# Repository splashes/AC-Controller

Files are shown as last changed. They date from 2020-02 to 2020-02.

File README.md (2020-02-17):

# P&S Power Electronics AC-Controller
Paul and sabrina AC-Controller and driver board

This is from P&S Power Electronics. I just got the files from them to upload it to GitHub so that whoever is searching for this awesome controller may get the necessary files in one place. Hope this helps someone.

This is the link for MPaulHomes https://github.com/MPaulHolmes

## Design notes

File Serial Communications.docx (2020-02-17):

Serial Communications

To get Realterm, go here:

https://sourceforge.net/projects/realterm/

Then, to set it up, connect the board to the computer with the USB plug. Usually, green is data+, white is data-, red is Vcc, and black is ground.

Next, connect the board to the power supply (The Nissan leaf board uses an external 12v, the chevy volt board uses 12v, the control/driver board uses 24v)

Then, run realterm.

On the “Display” tab, set “Rows” to 40, and click the “Scrollback” box and set it to 2000 for the scrollback.

Now, go to the “Port” tab, and change the “Baud” to 115200. The “Port” should already have detected the right port. Click the “Change” box, so that it will now have the baud rate updated.

Now, click on the black open text box area at the top, and hit enter. You should see a message like “Invalid command. Hit ‘?’ to see a list of valid commands”.

You are now ready to communicate!

current-sensor-amps-per-volt (not needed for the Leaf board/Leaf motor)

The way you use this is, if your current sensor has a feedback of 2.5 volts + 1 volt at “x” amps, then you would type:

current-sensor-amps-per-volt x

So, in the case of the LEM Hass 300-s, the datasheet says that at 0 amps, the current sensor feedback is 2.5v, and at 300 amps, the voltage is about 2.5v + 0.625v. So, the current sensor amps per volt is 300/0.625 amps = 480 amps. So, if you are using a LEM Hass 300-s, you would type:

current-sensor-amps-per-volt 480

If you are using one of the Nissan Leaf control boards with a stock Leaf controller, you would use 400. For the Chevy Volt stock controller, you would use 350.

run-pi-test2 (not needed for the leaf board/leaf motor)

This is the first test that must be done for the motor. It works on all motor types. Start with a battery pack voltage < 100vDC, but at least about 50vDC. If you have no idea about the motor’s characteristics, type

run-pi-test2

It will display a bunch of numbers that are from 0 to around 500. The goal is for the numbers to fall to zero quickly. So, the data might look like this (it always starts at zero. Ignore that one!):

0,500,498,425,402,356,322,300,288,233,188,130,89,63,22,-30,15,-25,44,-12,34,-55,27,…

That would be a good result. It quickly converged, in less than like 30 iterations to around zero. It’s OK that it bounces back and forth once it hits zero.

If you are using a Nissan Leaf motor and my Nissan Leaf control board, don’t worry about this.

kp/ki (not needed for the Leaf board/Leaf motor)

To change the proportional gain of the PI control loop for the torque control, type:

kp xxxxx

To change the integral gain of the PI control loop for torque control, type:

Ki xxxxx

where ‘xxxxx’ is a number from 1 up to 20000. Here’s an example of the usage:
kp 6200

ki 100

For best results, kp should be about 50 or 100 times bigger than ki. Once you have changed kp and ki to a new value, if you want, you can run ‘run-pi-test2’ to see if the results are good.

current-angle-offset

for motor type 2 (permanent magnet with encoder, with one index pulse per mechanical revolution), and motor type 3 (1 index pulse per electrical revolution, which is common when using a resolver. I use this setting for the Nissan Leaf motor and the Remy). The angle offset is the difference between the magnetic north of the motor and the index pulse of the position sensor. You can change it to be in the range of 0 to 511, where the circle is divided up into 512 “degrees”.

This is one of the configurations for the motor that must be done once to find the ideal angle offset. Before doing this procedure, you should find good Kp and Ki values. To do this, follow this procedure:

angle-offset 0

attempt to turn the motor with throttle

angle-offset 20

attempt to turn motor with throttle

…

Keep going until the motor changes directions. Then, reduce the angle offset until the motor no longer turns. The motor may not turn for a range of angle offsets. For example, like this:

angle-offset 138 makes the motor turn clockwise

angle-offset 139 makes the motor not turn at all

angle-offset 140 makes the motor not turn at all

…

angle-offset 163 makes the motor not turn at all

angle-offset 164 makes the motor turn COUNTER-clockwise.

The ideal angle offset for the motor NOT MOVING in this case would be (139 + 163)/2 = 151. What you have found is the absolute WORST angle offset for the motor. Now, to find the ideal angle offset, either add or subtract 128 (the scale is 512 “virtual degrees” in a circle, so 128 “virtual degrees” is the same as 90 real degrees). So, you would type:

angle-offset 279

Or

angle-offset 23

max-regen-position

min-regen-position

min-throttle-position

max-throttle-position

The throttle feedback to the controller will be a signal in 0 to 5v. The controller interprets that as a number from 0 to 1023. The throttle is similar to how they do it on a Tesla and the Nissan Leaf. For some range for the first few % of throttle, it is variable regenerative braking. Somewhere in the middle is zero torque command, and the last bit of throttle is variable positive torque command. So, it might be something like this:

max-regen-position 59

min-regen-position 150

min-throttle-position 220

max-throttle-position 942

100% throttle would be around 942 for the raw feedback, and 0% throttle would have a raw feedback of around 59. Zero torque command would be any raw value in 150 up to 220 in this case.

max-motor-amps

max-motor-amps-regen

This basically sets the maximum torque producing current (Iq) for a permanent magnet motor, and it sets the maximum Id and Iq for an induction motor. This is not battery current, but just current in the motor. You would use it like this:

max-motor-amps 300

max-motor-amps-regen 75

With those settings, you would see 300 amps for Iq in the motor when the throttle is at max-throttle-position. And at zero throttle, you would see -75amps for Iq. So, if you want your car to have very strong regen braking at zero throttle, set the max-motor-amps-regen to something very high. If you want to be thrown back in your seat at takeoff, set max-motor-amps to something very high.

max-battery-amps

max-battery-amps-regen

This sets the maximum current allowed to go into/out of the BATTERIES. You would use it like this:

max-battery-amps 200

max-battery-amps-regen 50

pole-pairs (not needed for the Leaf board/Leaf motor)

this is the number of pole pairs of the motor. One way to find out the number of pole pairs for a permanent magnet motor is to turn the motor shaft at 1 revolution per second, and then measure the Hz on 2 of the phases with a volt meter. It is used for finding the mechanical RPM. Usage:

pole-pairs 4

If you are using a Nissan Leaf motor, the number of pole pairs is 4. But this will already be set if you are using my Leaf control board replacement.

max-rpm

This sets the maximum RPM of the motor shaft. It will hit this, and then bounce against it like in a traditional car (“rev rev rev rev”). Usage:

max-rpm 4500

That would set the max RPM to 4500 RPM.

config

This just shows how the controller is currently configured. Pole pairs, throttle settings, etc… Usage:

config

precharge-time

This sets the time for the precharge delay, in tenths of a second. Example usage:

precharge-time 59

That would set the delay to 5.9 seconds from the time of closing the precharge relay to closing the main contactor. A very safe time delay is 5 RC time constants. The C is the capacitance of your bus capacitor. The R is the resistance of your precharge resistor. So, let’s say you have a bus capacitance of about 1200 microfarad. That means C = 0.0012 Farad. Also, let’s say you are using a 470 Ohm precharge resistor. Then, you would set the precharge time to 5*470*0.0012 seconds = 2.82 seconds. So, you would type:

precharge-time 29

save

One other thing to consider is the energy dissipated in the precharge resistor. You can’t just use any resistor. The total energy during precharge is 0.5 * C * V*V, where C is the bus capacitance, and V is the final bus voltage. Let’s say the bus voltage is 400 volts. So, in our example, the total energy through the resistor is 0.5 * 0.0012 * 400 * 400 Joules = 96 Joules. So, you would need to choose a resistor with a Joule rating greater than 96 Joules. Most resistors don’t list their joule rating, so I just use something from this family of resistors:

https://www.mouser.com/ProductDetail/Ohmite/AY821KE?qs=sGAEpiMZZMvmQ%252bOLa8n%2fMxoZ6mTh6DRODpV4zT6BJZY%3d

data-stream-period

This starts the datastream. You tell it the delay, in milliseconds. Example of usage:

data-stream-period 100

That will start streaming the data that has been enabled for streaming, and will stream it at 100ms intervals. To stop the datastream, type “off”.

stream-raw-throttle

This is one example of enabling something for streaming. This adds the raw throttle to the datastream. Usage:

stream-raw-throttle 1

If you want to remove raw throttle from the datastream, type:

stream-raw-throttle 0

There are lots of things that can be added to the stream. To see a list, type “?”.

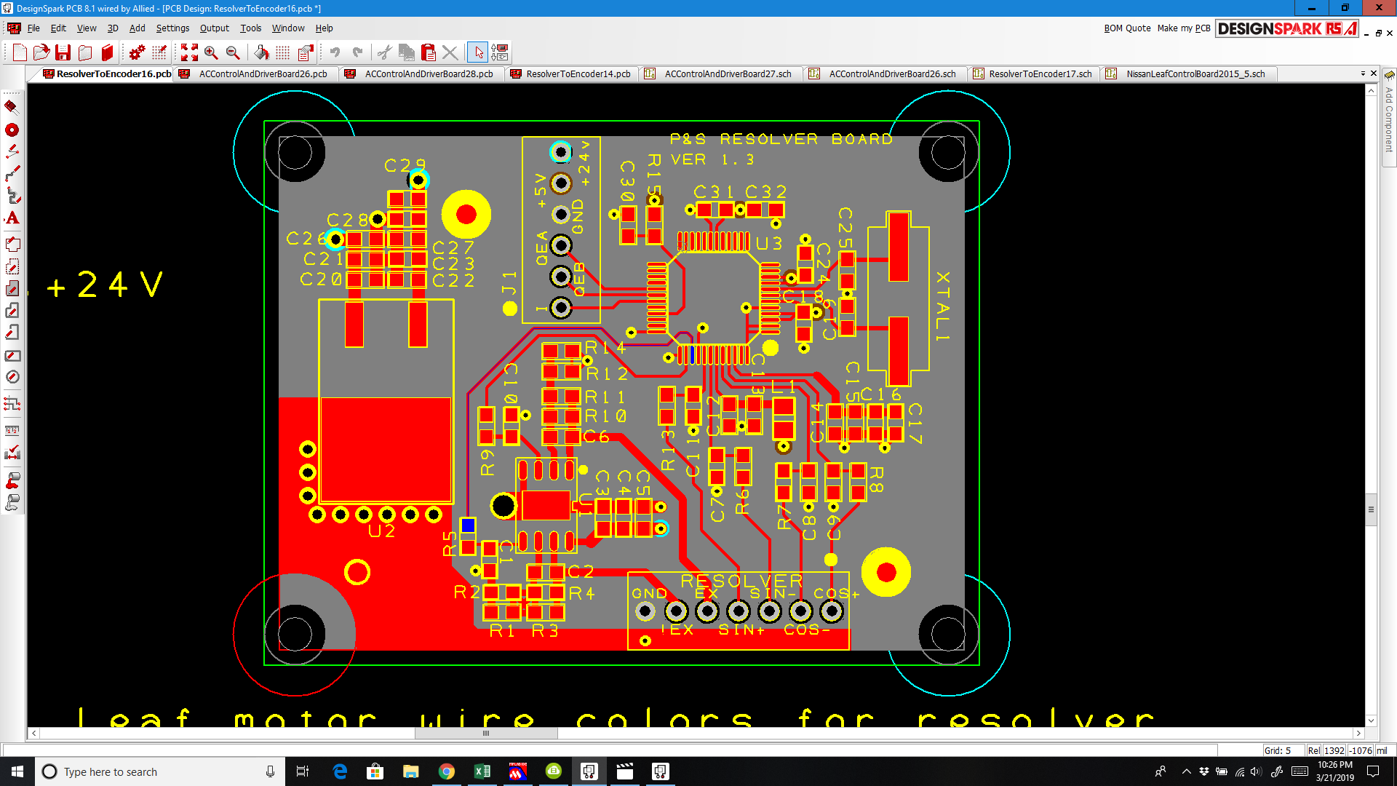
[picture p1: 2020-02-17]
ResolverToEncoder16.png

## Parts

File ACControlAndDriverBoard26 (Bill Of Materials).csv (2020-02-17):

Bill of Materials generated with DesignSpark PCB - www.DesignSpark.com/pcb
--------------------------------------------------------------------------
Ref Name | Component | Value | Package | MPN
Q11 | npn | BC846ALT1G | SOT23 | BC846ALT1G
Q9 | npn | BC846ALT1G | SOT23 | BC846ALT1G
J16 | 6 pin 2x3 |  | USER | 103777-3
U2 | 5v regulator |  | USER | R-78E5.0-1.0
U21 | ATTiny25 | ATTINY25-20SSU | soic8 | ATTINY25-20SSU
C103 | mlcc capacitor | 0.1uF | 1206Standard | C1206C104K5RACTU
C61 | mlcc capacitor | 0.1uF | 1206Standard | C1206C104K5RACTU
C52 | mlcc capacitor | 0.1uF | 1206Standard | C1206C104K5RACTU
C8 | mlcc capacitor | 0.1uF | 1206Standard | C1206C104K5RACTU
C9 | mlcc capacitor | 0.1uF | 1206Standard | C1206C104K5RACTU
C47 | mlcc capacitor | 0.1uF | 1206Standard | C1206C104K5RACTU
C25 | mlcc capacitor | 0.1uF | 1206Standard | C1206C104K5RACTU
C94 | mlcc capacitor | 0.1uF | 1206Standard | C1206C104K5RACTU
C59 | mlcc capacitor | 0.1uF | 1206Standard | C1206C104K5RACTU
C56 | mlcc capacitor | 0.1uF | 1206Standard | C1206C104K5RACTU
C74 | mlcc capacitor | 0.1uF | 1206Standard | C1206C104K5RACTU
C75 | mlcc capacitor | 0.1uF | 1206Standard | C1206C104K5RACTU
C90 | mlcc capacitor | 0.1uF | 1206Standard | C1206C104K5RACTU
C104 | mlcc capacitor | 0.1uF | 1206Standard | C1206C104K5RACTU
C100 | mlcc capacitor | 0.1uF | 1206Standard | C1206C104K5RACTU
C41 | mlcc capacitor | 0.1uF | 1206Standard | C1206C104K5RACTU
C72 | mlcc capacitor | 0.1uF | 1206Standard | C1206C104K5RACTU
C108 | mlcc capacitor | 0.1uF | 1206Standard | C1206C104K5RACTU
C123 | mlcc capacitor | 0.1uF | 1206Standard | C1206C104K5RACTU
C154 | mlcc capacitor | 0.1uF | 1206Standard | C1206C104K5RACTU
C30 | mlcc capacitor | 0.1uF | 1206Standard | C1206C104K5RACTU
C85 | mlcc capacitor | 0.1uF | 1206Standard | C1206C104K5RACTU
C7 | mlcc capacitor | 0.01uF | 1206Standard | 12065C103KAT4A
C42 | mlcc capacitor | 0.01uF | 1206Standard | 12065C103KAT4A
C71 | mlcc capacitor | 0.01uF | 1206Standard | 12065C103KAT4A
C110 | mlcc capacitor | 0.01uF | 1206Standard | 12065C103KAT4A
C122 | mlcc capacitor | 0.01uF | 1206Standard | 12065C103KAT4A
C155 | mlcc capacitor | 0.01uF | 1206Standard | 12065C103KAT4A
C73 | mlcc capacitor | 0.01uF | 1206Standard | 12065C103KAT4A
C60 | mlcc capacitor | 0.01uF | 1206Standard | 12065C103KAT4A
C62 | mlcc capacitor | 0.01uF | 1206Standard | 12065C103KAT4A
C126 | mlcc capacitor | 0.01uF | 1206Standard | 12065C103KAT4A
C6 | mlcc capacitor | 0.01uF | 1206Standard | 12065C103KAT4A
C10 | mlcc capacitor | 0.01uF | 1206Standard | 12065C103KAT4A
C111 | mlcc capacitor | 0.01uF | 1206Standard | 12065C103KAT4A
C95 | mlcc capacitor | 0.01uF | 1206Standard | 12065C103KAT4A
C134 | mlcc capacitor | 0.01uF | 1206Standard | 12065C103KAT4A
C117 | mlcc capacitor | 0.01uF | 1206Standard | 12065C103KAT4A
C109 | mlcc capacitor | 4.7uF 50v | 1206Standard | CGA5L3X7R1H475K160AB
C23 | mlcc capacitor | 4.7uF 50v | 1206Standard | CGA5L3X7R1H475K160AB
C13 | mlcc capacitor | 4.7uF 50v | 1206Standard | CGA5L3X7R1H475K160AB
C16 | mlcc capacitor | 4.7uF 50v | 1206Standard | CGA5L3X7R1H475K160AB
C18 | mlcc capacitor | 4.7uF 50v | 1206Standard | CGA5L3X7R1H475K160AB
C15 | mlcc capacitor | 4.7uF 50v | 1206Standard | CGA5L3X7R1H475K160AB
C12 | mlcc capacitor | 4.7uF 50v | 1206Standard | CGA5L3X7R1H475K160AB
C37 | mlcc capacitor | 4.7uF 50v | 1206Standard | CGA5L3X7R1H475K160AB
C39 | mlcc capacitor | 4.7uF 50v | 1206Standard | CGA5L3X7R1H475K160AB
C40 | mlcc capacitor | 4.7uF 50v | 1206Standard | CGA5L3X7R1H475K160AB
C36 | mlcc capacitor | 4.7uF 50v | 1206Standard | CGA5L3X7R1H475K160AB
C33 | mlcc capacitor | 4.7uF 50v | 1206Standard | CGA5L3X7R1H475K160AB
C32 | mlcc capacitor | 4.7uF 50v | 1206Standard | CGA5L3X7R1H475K160AB
C77 | mlcc capacitor | 4.7uF 50v | 1206Standard | CGA5L3X7R1H475K160AB
C83 | mlcc capacitor | 4.7uF 50v | 1206Standard | CGA5L3X7R1H475K160AB
C76 | mlcc capacitor | 4.7uF 50v | 1206Standard | CGA5L3X7R1H475K160AB
C79 | mlcc capacitor | 4.7uF 50v | 1206Standard | CGA5L3X7R1H475K160AB
C98 | mlcc capacitor | 4.7uF 50v | 1206Standard | CGA5L3X7R1H475K160AB
C106 | mlcc capacitor | 4.7uF 50v | 1206Standard | CGA5L3X7R1H475K160AB
C105 | mlcc capacitor | 4.7uF 50v | 1206Standard | CGA5L3X7R1H475K160AB
C97 | mlcc capacitor | 4.7uF 50v | 1206Standard | CGA5L3X7R1H475K160AB
C99 | mlcc capacitor | 4.7uF 50v | 1206Standard | CGA5L3X7R1H475K160AB
C101 | mlcc capacitor | 4.7uF 50v | 1206Standard | CGA5L3X7R1H475K160AB
C84 | mlcc capacitor | 4.7uF 50v | 1206Standard | CGA5L3X7R1H475K160AB
C80 | mlcc capacitor | 4.7uF 50v | 1206Standard | CGA5L3X7R1H475K160AB
C130 | mlcc capacitor | 4.7uF 50v | 1206Standard | CGA5L3X7R1H475K160AB
C127 | mlcc capacitor | 4.7uF 50v | 1206Standard | CGA5L3X7R1H475K160AB
C135 | mlcc capacitor | 4.7uF 50v | 1206Standard | CGA5L3X7R1H475K160AB
C150 | mlcc capacitor | 4.7uF 50v | 1206Standard | CGA5L3X7R1H475K160AB
C148 | mlcc capacitor | 4.7uF 50v | 1206Standard | CGA5L3X7R1H475K160AB
C153 | mlcc capacitor | 4.7uF 50v | 1206Standard | CGA5L3X7R1H475K160AB
C146 | mlcc capacitor | 4.7uF 50v | 1206Standard | CGA5L3X7R1H475K160AB
C147 | mlcc capacitor | 4.7uF 50v | 1206Standard | CGA5L3X7R1H475K160AB
C149 | mlcc capacitor | 4.7uF 50v | 1206Standard | CGA5L3X7R1H475K160AB
C19 | mlcc capacitor | 4.7uF 50v | 1206Standard | CGA5L3X7R1H475K160AB
C24 | mlcc capacitor | 4.7uF 50v | 1206Standard | CGA5L3X7R1H475K160AB
C34 | mlcc capacitor | 4.7uF 50v | 1206Standard | CGA5L3X7R1H475K160AB
C89 | mlcc capacitor | 4.7uF 50v | 1206Standard | CGA5L3X7R1H475K160AB
C88 | mlcc capacitor | 4.7uF 50v | 1206Standard | CGA5L3X7R1H475K160AB
C102 | mlcc capacitor | 4.7uF 50v | 1206Standard | CGA5L3X7R1H475K160AB
C107 | mlcc capacitor | 4.7uF 50v | 1206Standard | CGA5L3X7R1H475K160AB
C141 | mlcc capacitor | 4.7uF 50v | 1206Standard | CGA5L3X7R1H475K160AB
C152 | mlcc capacitor | 4.7uF 50v | 1206Standard | CGA5L3X7R1H475K160AB
C151 | mlcc capacitor | 4.7uF 50v | 1206Standard | CGA5L3X7R1H475K160AB
C82 | mlcc capacitor | 4.7uF 50v | 1206Standard | CGA5L3X7R1H475K160AB
C65 | mlcc capacitor | 4.7uF 50v | 1206Standard | CGA5L3X7R1H475K160AB
C67 | mlcc capacitor | 4.7uF 50v | 1206Standard | CGA5L3X7R1H475K160AB
C55 | mlcc capacitor | 4.7uF 50v | 1206Standard | CGA5L3X7R1H475K160AB
C128 | mlcc capacitor | 4.7uF 50v | 1206Standard | CGA5L3X7R1H475K160AB
C131 | mlcc capacitor | 4.7uF 50v | 1206Standard | CGA5L3X7R1H475K160AB
C136 | mlcc capacitor | 4.7uF 50v | 1206Standard | CGA5L3X7R1H475K160AB
C140 | mlcc capacitor | 4.7uF 50v | 1206Standard | CGA5L3X7R1H475K160AB
C133 | mlcc capacitor | 4.7uF 50v | 1206Standard | CGA5L3X7R1H475K160AB
C22 | mlcc capacitor | 4.7uF 50v | 1206Standard | CGA5L3X7R1H475K160AB
C21 | mlcc capacitor | 4.7uF 50v | 1206Standard | CGA5L3X7R1H475K160AB
C28 | mlcc capacitor | 4.7uF 50v | 1206Standard | CGA5L3X7R1H475K160AB
C27 | mlcc capacitor | 4.7uF 50v | 1206Standard | CGA5L3X7R1H475K160AB
C86 | mlcc capacitor | 4.7uF 50v | 1206Standard | CGA5L3X7R1H475K160AB
C87 | mlcc capacitor | 4.7uF 50v | 1206Standard | CGA5L3X7R1H475K160AB
C92 | mlcc capacitor | 4.7uF 50v | 1206Standard | CGA5L3X7R1H475K160AB
C91 | mlcc capacitor | 4.7uF 50v | 1206Standard | CGA5L3X7R1H475K160AB
C138 | mlcc capacitor | 4.7uF 50v | 1206Standard | CGA5L3X7R1H475K160AB
C139 | mlcc capacitor | 4.7uF 50v | 1206Standard | CGA5L3X7R1H475K160AB
C144 | mlcc capacitor | 4.7uF 50v | 1206Standard | CGA5L3X7R1H475K160AB
C143 | mlcc capacitor | 4.7uF 50v | 1206Standard | CGA5L3X7R1H475K160AB
C45 | mlcc capacitor | 4.7uF 50v | 1206Standard | CGA5L3X7R1H475K160AB
C31 | mlcc capacitor | 4.7uF 50v | 1206Standard | CGA5L3X7R1H475K160AB
C20 | mlcc capacitor | 4.7uF 50v | 1206Standard | CGA5L3X7R1H475K160AB
C96 | mlcc capacitor | 4.7uF 50v | 1206Standard | CGA5L3X7R1H475K160AB
C124 | mlcc capacitor | 4.7uF 50v | 1206Standard | CGA5L3X7R1H475K160AB
C11 | mlcc capacitor | 4.7uF 50v | 1206Standard | CGA5L3X7R1H475K160AB
C35 | mlcc capacitor | 4.7uF 50v | 1206Standard | CGA5L3X7R1H475K160AB
C44 | mlcc capacitor | 4.7uF 50v | 1206Standard | CGA5L3X7R1H475K160AB
C46 | mlcc capacitor | 4.7uF 50v | 1206Standard | CGA5L3X7R1H475K160AB
C81 | mlcc capacitor | 4.7uF 50v | 1206Standard | CGA5L3X7R1H475K160AB
C26 | mlcc capacitor | 4.7uF 50v | 1206Standard | CGA5L3X7R1H475K160AB
C2 | mlcc capacitor | 4.7uF 50v | 1206Standard | CGA5L3X7R1H475K160AB
C48 | mlcc capacitor | 4.7uF 50v | 1206Standard | CGA5L3X7R1H475K160AB
C63 | mlcc capacitor | 4.7uF 50v | 1206Standard | CGA5L3X7R1H475K160AB
C162 | mlcc capacitor | 4.7uF 50v | 1206Standard | CGA5L3X7R1H475K160AB
C17 | mlcc capacitor | 4.7uF 50v | 1206Standard | CGA5L3X7R1H475K160AB
C113 | mlcc capacitor | 4.7uF 50v | 1206Standard | CGA5L3X7R1H475K160AB
C132 | mlcc capacitor | 4.7uF 50v | 1206Standard | CGA5L3X7R1H475K160AB
C157 | mlcc capacitor | 4.7uF 50v | 1206Standard | CGA5L3X7R1H475K160AB
C51 | mlcc capacitor | 4.7uF 50v | 1206Standard | CGA5L3X7R1H475K160AB
C64 | mlcc capacitor | 4.7uF 50v | 1206Standard | CGA5L3X7R1H475K160AB
C115 | mlcc capacitor | 4.7uF 50v | 1206Standard | CGA5L3X7R1H475K160AB
C119 | mlcc capacitor | 4.7uF 50v | 1206Standard | CGA5L3X7R1H475K160AB
C161 | mlcc capacitor | 4.7uF 50v | 1206Standard | CGA5L3X7R1H475K160AB
C163 | mlcc capacitor | 4.7uF 50v | 1206Standard | CGA5L3X7R1H475K160AB
C49 | mlcc capacitor | 4.7uF 50v | 1206Standard | CGA5L3X7R1H475K160AB
C68 | mlcc capacitor | 4.7uF 50v | 1206Standard | CGA5L3X7R1H475K160AB
C116 | mlcc capacitor | 4.7uF 50v | 1206Standard | CGA5L3X7R1H475K160AB
C120 | mlcc capacitor | 4.7uF 50v | 1206Standard | CGA5L3X7R1H475K160AB
C159 | mlcc capacitor | 4.7uF 50v | 1206Standard | CGA5L3X7R1H475K160AB
C125 | mlcc capacitor | 4.7uF 50v | 1206Standard | CGA5L3X7R1H475K160AB
C114 | mlcc capacitor | 4.7uF 50v | 1206Standard | CGA5L3X7R1H475K160AB
C118 | mlcc capacitor | 4.7uF 50v | 1206Standard | CGA5L3X7R1H475K160AB
C158 | mlcc capacitor | 4.7uF 50v | 1206Standard | CGA5L3X7R1H475K160AB
C38 | mlcc capacitor | 4.7uF 50v | 1206Standard | CGA5L3X7R1H475K160AB
C66 | mlcc capacitor | 30pF | 1206Standard | C1206C300J5GACTU
C70 | mlcc capacitor | 30pF | 1206Standard | C1206C300J5GACTU
C5 | mlcc capacitor | 100pF | 1206Standard | CC1206JRNPO9BN101
C69 | mlcc capacitor | 100pF | 1206Standard | CC1206JRNPO9BN101
C93 | mlcc capacitor | 100pF | 1206Standard | CC1206JRNPO9BN101
C121 | mlcc capacitor | 100pF | 1206Standard | CC1206JRNPO9BN101
C145 | mlcc capacitor | 100pF | 1206Standard | CC1206JRNPO9BN101
C29 | mlcc capacitor | 100pF | 1206Standard | CC1206JRNPO9BN101
C14 | mlcc capacitor | 330pF | 1206Standard | VJ1206Y331KXXCW1BC
C43 | mlcc capacitor | 330pF | 1206Standard | VJ1206Y331KXXCW1BC
C78 | mlcc capacitor | 330pF | 1206Standard | VJ1206Y331KXXCW1BC
C112 | mlcc capacitor | 330pF | 1206Standard | VJ1206Y331KXXCW1BC
C129 | mlcc capacitor | 330pF | 1206Standard | VJ1206Y331KXXCW1BC
C156 | mlcc capacitor | 330pF | 1206Standard | VJ1206Y331KXXCW1BC
C57 | mlcc capacitor | 330pF | 1206Standard | VJ1206Y331KXXCW1BC
C53 | mlcc capacitor | 330pF | 1206Standard | VJ1206Y331KXXCW1BC
C142 | mlcc capacitor | 330pF | 1206Standard | VJ1206Y331KXXCW1BC
C137 | mlcc capacitor | 330pF | 1206Standard | VJ1206Y331KXXCW1BC
C50 | mlcc capacitor | xxx | 1206Standard | DO NOT POPULATE
C54 | mlcc capacitor | xxx | 1206Standard | DO NOT POPULATE
C58 | mlcc capacitor | xxx | 1206Standard | DO NOT POPULATE
C1 | mlcc capacitor | xxx | 1206Standard | DO NOT POPULATE
C160 | mlcc capacitor | xxx | 1206Standard | DO NOT POPULATE
C3 | electrolytic cap | 150-220uF 25v | cap015LS | UHE1E221MPD
C4 | electrolytic cap | 470uF 50v | USER | UPW1H471MHD
L1 | ChokeCommonMode |  |  | SRF0905-102Y
XTAL1 | crystal | 7.3728MHz 20pF |  | ECS-73-20-4XDN
U3 | dc-dc converter | MEV1S2405 |  | MEV1S2405SC
D23 | schottky diode | SS26FL | SOD123w | SS26FL
D28 | schottky diode | SS26FL | SOD123w | SS26FL
D27 | schottky diode | SS26FL | SOD123w | SS26FL
D24 | schottky diode | SS26FL | SOD123w | SS26FL
U18 | dspic30f4011 | DSPIC30F4011-30I/PT | TQFP44 | DSPIC30F4011-30I/PT
U23 | FTDI_FT232RL |  | SSOP | FT232RL-REEL
F1 | Fuse | AF1206F1.60TM | 1206 | AF1206F1.60TM
U6 | GateDriveOptoWithReset | FOD8316 | SOIC16 | FOD8316R2V
U11 | GateDriveOptoWithReset | FOD8316 | SOIC16 | FOD8316R2V
U24 | GateDriveOptoWithReset | FOD8316 | SOIC16 | FOD8316R2V
U19 | GateDriveOptoWithReset | FOD8316 | SOIC16 | FOD8316R2V
U33 | GateDriveOptoWithReset | FOD8316 | SOIC16 | FOD8316R2V
U29 | GateDriveOptoWithReset | FOD8316 | SOIC16 | FOD8316R2V
U31 | HCNR200 | HCNR200-300E | GullWing | HCNR200-300E
ISP | ISP-Interface |  | USER | 3-644456-6
ENCODER | 6 pin male |  | USER | 22-04-1061
 | 6 pin female |  |  | 22-01-1062
U1 | dual mosfet driver | IXDI604SI | soic8_heat_tab | IXDI604SI
U14 | dual mosfet driver | IXDI604SI | soic8_heat_tab | IXDI604SI
U16 | dual mosfet driver | IXDI604SI | soic8_heat_tab | IXDI604SI
U25 | dual mosfet driver | IXDI604SI | soic8_heat_tab | IXDI604SI
U27 | dual mosfet driver | IXDI604SI | soic8_heat_tab | IXDI604SI
U34 | dual mosfet driver | IXDI604SI | soic8_heat_tab | IXDI604SI
CURR1 | 3 pin connector | 3pin Vert Lock | USER | 22-04-1031
CURR3 | 3 pin connector | 3pin Vert Lock | USER | 22-04-1031
CURR2 | 3 pin connector | 3pin Vert Lock | USER | 22-04-1031
TEMP | 3 pin connector | 3pin Vert Lock | USER | 22-04-1031
REV | 3 pin connector | 3pin Vert Lock | USER | 22-04-1031
CAN | 3 pin connector | 3pin Vert Lock | USER | 22-04-1031
BRK | 3 pin connector | 3pin Vert Lock | USER | 22-04-1031
THR | 3 pin connector | 3pin Vert Lock | USER | 22-04-1031
 | female housing 2 OF THESE!! |  |  | 10-11-2153
TRANS1 | Line Filter |  | 13x10mmHoles | PLA10AS3021R3R2B
TRANS2 | Line Filter |  | 13x10mmHoles | PLA10AS3021R3R2B
TRANS3 | Line Filter |  | 13x10mmHoles | PLA10AS3021R3R2B
TRANS4 | Line Filter |  | 13x10mmHoles | PLA10AS3021R3R2B
TRANS5 | Line Filter |  | 13x10mmHoles | PLA10AS3021R3R2B
TRANS6 | Line Filter |  | 13x10mmHoles | PLA10AS3021R3R2B
U5 | comparator | LM293DR | soic8 | LM293DR
U10 | comparator | LM293DR | soic8 | LM293DR
U13 | comparator | LM293DR | soic8 | LM293DR
U8 | comparator | LM293DR | soic8 | LM293DR
U37 | 2.5v voltage regulator | LM4040C25IDBZR | SOT23 | LM4040C25IDBZR
U4 | Quad 2 input NAND |  | SOIC14 | MC74HC00ADR2G
U20 | CAN Transceiver | MCP2551-I/SN | SOIC8 | MCP2551-I/SN
Q1 | NPNTrans | MJD44H11T4 | dpakStandard | MJD44H11T4
Q4 | NPNTrans | MJD44H11T4 | dpakStandard | MJD44H11T5
Q5 | NPNTrans | MJD44H11T4 | dpakStandard | MJD44H11T6
Q10 | NPNTrans | MJD44H11T4 | dpakStandard | MJD44H11T7
Q14 | NPNTrans | MJD44H11T4 | dpakStandard | MJD44H11T8
Q8 | NPNTrans | MJD44H11T4 | dpakStandard | MJD44H11T9
U32 | op amp |  | soic8 | MCP6241T-E/SN
U30 | op amp |  | soic8 | MCP6241T-E/SN
Q2 | PNPTRANS | MJD45H11T4G | dpakStandard | MJD45H11T4G
Q3 | PNPTRANS | MJD45H11T4G | dpakStandard | MJD45H11T4G
Q6 | PNPTRANS | MJD45H11T4G | dpakStandard | MJD45H11T4G
Q7 | PNPTRANS | MJD45H11T4G | dpakStandard | MJD45H11T4G
Q12 | PNPTRANS | MJD45H11T4G | dpakStandard | MJD45H11T4G
Q13 | PNPTRANS | MJD45H11T4G | dpakStandard | MJD45H11T4G
U36 | schottky bridge rectifier |  | SurfaceMount | CDBHM260L-HF
U15 | schottky bridge rectifier |  | SurfaceMount | CDBHM260L-HF
U17 | schottky bridge rectifier |  | SurfaceMount | CDBHM260L-HF
U26 | schottky bridge rectifier |  | SurfaceMount | CDBHM260L-HF
U28 | schottky bridge rectifier |  | SurfaceMount | CDBHM260L-HF
U35 | schottky bridge rectifier |  | SurfaceMount | CDBHM260L-HF
RELAY2 | Relay SPST 1FormA |  | User | G5Q-1A-EL-HA-VH DC24
RELAY1 | Relay SPST 1FormA |  | User | G5Q-1A-EL-HA-VH DC24
R62 | resistor | 1k | 1206Standard | RK73H2BTTE1001F
R38 | resistor | 1k | 1206Standard | RK73H2BTTE1001F
R39 | resistor | 1k | 1206Standard | RK73H2BTTE1001F
R40 | resistor | 1k | 1206Standard | RK73H2BTTE1001F
R41 | resistor | 1k | 1206Standard | RK73H2BTTE1001F
R42 | resistor | 1k | 1206Standard | RK73H2BTTE1001F
R44 | resistor | 1k | 1206Standard | RK73H2BTTE1001F
R45 | resistor | 1k | 1206Standard | RK73H2BTTE1001F
R18 | resistor | 1k | 1206Standard | RK73H2BTTE1001F
R25 | resistor | 1k | 1206Standard | RK73H2BTTE1001F
R60 | resistor | 1k | 1206Standard | RK73H2BTTE1001F
R84 | resistor | 1k | 1206Standard | RK73H2BTTE1001F
R105 | resistor | 2k | 1206Standard | RC1206FR-072KL
R106 | resistor | 2k | 1206Standard | RC1206FR-072KL
R108 | resistor | 2k | 1206Standard | RC1206FR-072KL
R19 | resistor | 2k | 1206Standard | RC1206FR-072KL
R22 | resistor | 2k | 1206Standard | RC1206FR-072KL
R27 | resistor | 2k | 1206Standard | RC1206FR-072KL
R29 | resistor | 2k | 1206Standard | RC1206FR-072KL
R113 | resistor | 2k | 1206Standard | RC1206FR-072KL
R16 | resistor | 2k | 1206Standard | RC1206FR-072KL
R102 | resistor | 2.7 | 1210 | SG73P2ETTD2R70F
R37 | resistor | 2.7 | 1210 | SG73P2ETTD2R70F
R52 | resistor | 2.7 | 1210 | SG73P2ETTD2R70F
R72 | resistor | 2.7 | 1210 | SG73P2ETTD2R70F
R75 | resistor | 2.7 | 1210 | SG73P2ETTD2R70F
R100 | resistor | 2.7 | 1210 | SG73P2ETTD2R70F
R111 | resistor | 2.8k | 1206Standard | RC1206FR-072K8L
R15 | resistor | 3k | 1206Standard | RK73H2BTTD3001F
R24 | resistor | 3k | 1206Standard | RK73H2BTTD3001F
R61 | resistor | 3k | 1206Standard | RK73H2BTTD3001F
R66 | resistor | 3k | 1206Standard | RK73H2BTTD3001F
R80 | resistor | 3k | 1206Standard | RK73H2BTTD3001F
R87 | resistor | 3k | 1206Standard | RK73H2BTTD3001F
R3 | resistor | 3.3Ohm 1w | R0800 | PCF1C3R3K
R4 | resistor | 3.3Ohm 1w | R0800 | PCF1C3R3K
R6 | resistor | 3.3Ohm 1w | R0800 | PCF1C3R3K
R5 | resistor | 3.3Ohm 1w | R0800 | PCF1C3R3K
R7 | resistor | 3.3Ohm 1w | R0800 | PCF1C3R3K
R8 | resistor | 3.3Ohm 1w | R0800 | PCF1C3R3K
R10 | resistor | 3.3Ohm 1w | R0800 | PCF1C3R3K
R9 | resistor | 3.3Ohm 1w | R0800 | PCF1C3R3K
R11 | resistor | 3.3Ohm 1w | R0800 | PCF1C3R3K
R12 | resistor | 3.3Ohm 1w | R0800 | PCF1C3R3K
R14 | resistor | 3.3Ohm 1w | R0800 | PCF1C3R3K
R13 | resistor | 3.3Ohm 1w | R0800 | PCF1C3R3K
R103 | resistor | 3.92k | 1206Standard | RC1206FR-073K92L
R104 | resistor | 4.7k | 1206Standard | RC1206FR-074K7L
R51 | resistor | 4.7k | 1206Standard | RC1206FR-074K7L
R65 | resistor | 4.7k | 1206Standard | RC1206FR-074K7L
R43 | resistor | 4.7k | 1206Standard | RC1206FR-074K7L
R76 | resistor | 4.7k | 1206Standard | RC1206FR-074K7L
R73 | resistor | 4.7k | 1206Standard | RC1206FR-074K7L
R57 | resistor | 4.7k | 1206Standard | RC1206FR-074K7L
R49 | resistor | 4.7k | 1206Standard | RC1206FR-074K7L
R67 | resistor | 4.7k | 1206Standard | RC1206FR-074K7L
R20 | resistor | 4.7k | 1206Standard | RC1206FR-074K7L
R26 | resistor | 4.7k | 1206Standard | RC1206FR-074K7L
R107 | resistor | 10 | 1210 | ESR25JZPF10R0
R31 | resistor | 10 | 1210 | ESR25JZPF10R0
R54 | resistor | 10 | 1210 | ESR25JZPF10R0
R70 | resistor | 10 | 1210 | ESR25JZPF10R0
R77 | resistor | 10 | 1210 | ESR25JZPF10R0
R95 | resistor | 10 | 1210 | ESR25JZPF10R0
R30 | resistor | 10k | 1206Standard | RC1206FR-0710KL
R23 | resistor | 10k | 1206Standard | RC1206FR-0710KL
R63 | resistor | 10k | 1206Standard | RC1206FR-0710KL
R110 | resistor | 10k | 1206Standard | RC1206FR-0710KL
R17 | resistor | 10k | 1206Standard | RC1206FR-0710KL
R28 | resistor | 10k | 1206Standard | RC1206FR-0710KL
R56 | resistor | 10k | 1206Standard | RC1206FR-0710KL
R68 | resistor | 10k | 1206Standard | RC1206FR-0710KL
R79 | resistor | 10k | 1206Standard | RC1206FR-0710KL
R91 | resistor | 10k | 1206Standard | RC1206FR-0710KL
R58 | resistor | 10k | 1206Standard | RC1206FR-0710KL
R69 | resistor | 10k | 1206Standard | RC1206FR-0710KL
R112 | resistor | 22k | 1206Standard | RC1206FR-0722KL
R92 | resistor | 27k | 1210Standard | RC1210FR-0727KL
R90 | resistor | 27k | 1210Standard | RC1210FR-0727KL
R89 | resistor | 27k | 1210Standard | RC1210FR-0727KL
R94 | resistor | 27k | 1210Standard | RC1210FR-0727KL
R99 | resistor | 27k | 1210Standard | RC1210FR-0727KL
R97 | resistor | 27k | 1210Standard | RC1210FR-0727KL
R88 | resistor | 27k | 1210Standard | RC1210FR-0727KL
R86 | resistor | 27k | 1210Standard | RC1210FR-0727KL
R96 | resistor | 27k | 1210Standard | RC1210FR-0727KL
R93 | resistor | 27k | 1210Standard | RC1210FR-0727KL
R109 | resistor | 47k | 1206Standard | RC1206FR-0747KL
R32 | resistor | 47k | 1206Standard | RC1206FR-0747KL
R55 | resistor | 47k | 1206Standard | RC1206FR-0747KL
R71 | resistor | 47k | 1206Standard | RC1206FR-0747KL
R78 | resistor | 47k | 1206Standard | RC1206FR-0747KL
R98 | resistor | 47k | 1206Standard | RC1206FR-0747KL
R34 | resistor | 47k | 1206Standard | RC1206FR-0747KL
R47 | resistor | 47k | 1206Standard | RC1206FR-0747KL
R85 | resistor | 47k | 1206Standard | RC1206FR-0747KL
R81 | resistor | 47k | 1206Standard | RC1206FR-0747KL
R59 | resistor | 47k | 1206Standard | RC1206FR-0747KL
R46 | resistor | 47k | 1206Standard | RC1206FR-0747KL
R48 | resistor | 47k | 1206Standard | RC1206FR-0747KL
R35 | resistor | 47k | 1206Standard | RC1206FR-0747KL
R36 | resistor | 47k | 1206Standard | RC1206FR-0747KL
R33 | resistor | 47k | 1206Standard | RC1206FR-0747KL
R2 | resistor | 100 | 1206Standard | RC1206FR-07100RL
R21 | resistor | 100 | 1206Standard | RC1206FR-07100RL
R50 | resistor | 100 | 1206Standard | RC1206FR-07100RL
R64 | resistor | 100 | 1206Standard | RC1206FR-07100RL
R74 | resistor | 100 | 1206Standard | RC1206FR-07100RL
R83 | resistor | 100 | 1206Standard | RC1206FR-07100RL
R53 | resistor | 120 Ohm | 1210Standard | RC1210FR-07120RL
R82 | resistor | 330 | 1206Standard | RC1206FR-07330RL
R1 | resistor | xxx | 1206Standard | DO NOT POPULATE
R101 | resistor | xxx | 1206Standard | DO NOT POPULATE
U12 | SN74HC08 | SN74HC08D | SO14NB | SN74HC08D
U22 | SN74HC08 | SN74HC08D | SO14NB | SN74HC08D
U7 | SN74HC21 | SN74HC21D | SO14NB | SN74HC21D
U9 | SN74HC21 | SN74HC21D | SO14NB | SN74HC21D
J14 | SpadeConnector |  | FEMALE_0-11 | 534-3534 | mouser part number
J4 | SpadeConnector |  | FEMALE_0-11 | 534-3534 | mouser part number
J15 | SpadeConnector |  | FEMALE_0-11 | 534-3534 | mouser part number
J1 | SpadeConnector |  | FEMALE_0-11 | 534-3534 | mouser part number
J2 | SpadeConnector |  | FEMALE_0-11 | 534-3534 | mouser part number
J5 | SpadeConnector |  | FEMALE_0-11 | 534-3534 | mouser part number
J3 | SpadeConnector |  | FEMALE_0-11 | 534-3534 | mouser part number
J8 | SpadeConnector |  | FEMALE_0-11 | 534-3534 | mouser part number
J6 | SpadeConnector |  | FEMALE_0-11 | 534-3534 | mouser part number
J7 | SpadeConnector |  | FEMALE_0-11 | 534-3534 | mouser part number
J9 | SpadeConnector |  | FEMALE_0-11 | 534-3534 | mouser part number
J12 | SpadeConnector |  | FEMALE_0-11 | 534-3534 | mouser part number
J10 | SpadeConnector |  | FEMALE_0-11 | 534-3534 | mouser part number
J11 | SpadeConnector |  | FEMALE_0-11 | 534-3534 | mouser part number
J13 | SpadeConnector |  | FEMALE_0-11 | 534-3534 | mouser part number
VIN | SpadeConnector |  | FEMALE_0-11 | 534-3534 | mouser part number
GND | SpadeConnector |  | FEMALE_0-11 | 534-3534 | mouser part number
CIN | SpadeConnector |  | FEMALE_0-11 | 534-3534 | mouser part number
PCOUT | SpadeConnector |  | FEMALE_0-11 | 534-3534 | mouser part number
COUT | SpadeConnector |  | FEMALE_0-11 | 534-3534 | mouser part number
HVGND | SpadeConnector |  | FEMALE_0-11 | 534-3534 | mouser part number
HV | SpadeConnector |  | FEMALE_0-11 | 534-3534 | mouser part number
D1 | diode | 1000V Ultrafast | 0_45Inch | UF4007
D6 | diode | 1000V Ultrafast | 0_45Inch | UF4007
D11 | diode | 1000V Ultrafast | 0_45Inch | UF4007
D16 | diode | 1000V Ultrafast | 0_45Inch | UF4007
D25 | diode | 1000V Ultrafast | 0_45Inch | UF4007
D32 | diode | 1000V Ultrafast | 0_45Inch | UF4007
USB | USB_TYPE_B |  | USER | 67068-8110
D3 | ZenerDiode | 8.2v 5w | SMB | 3SMAJ5923B-TP
D9 | ZenerDiode | 8.2v 5w | SMB | 3SMAJ5923B-TP
D13 | ZenerDiode | 8.2v 5w | SMB | 3SMAJ5923B-TP
D19 | ZenerDiode | 8.2v 5w | SMB | 3SMAJ5923B-TP
D29 | ZenerDiode | 8.2v 5w | SMB | 3SMAJ5923B-TP
D35 | ZenerDiode | 8.2v 5w | SMB | 3SMAJ5923B-TP
D7 | ZenerDiode | 17V 5W | SMB | 1SMB5930BT3G
D15 | ZenerDiode | 17V 5W | SMB | 1SMB5930BT3G
D33 | ZenerDiode | 17V 5W | SMB | 1SMB5930BT3G
D31 | ZenerDiode | 17V 5W | SMB | 1SMB5930BT3G
D17 | ZenerDiode | 17V 5W | SMB | 1SMB5930BT3G
D5 | ZenerDiode | 17V 5W | SMB | 1SMB5930BT3G
D4 | ZenerDiode | 17V 5W | SMB | 1SMB5930BT3G
D8 | ZenerDiode | 17V 5W | SMB | 1SMB5930BT3G
D18 | ZenerDiode | 17V 5W | SMB | 1SMB5930BT3G
D14 | ZenerDiode | 17V 5W | SMB | 1SMB5930BT3G
D34 | ZenerDiode | 17V 5W | SMB | 1SMB5930BT3G
D30 | ZenerDiode | 17V 5W | SMB | 1SMB5930BT3G
D2 | ZenerDiode | 24v Zener | SMB | 1SMB5934BT3G
D10 | ZenerDiode | 24v Zener | SMB | 1SMB5934BT3G
D12 | ZenerDiode | 24v Zener | SMB | 1SMB5934BT3G
D22 | ZenerDiode | 24v Zener | SMB | 1SMB5934BT3G
D26 | ZenerDiode | 24v Zener | SMB | 1SMB5934BT3G
D36 | ZenerDiode | 24v Zener | SMB | 1SMB5934BT3G
D20 | schottky diode | MBRAF360T3G | SMB | MBRAF360T3G
D21 | TVS diode | SMA6J24A-TP | SMB | SMA6J24A-TP

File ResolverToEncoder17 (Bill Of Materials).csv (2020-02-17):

Bill of Materials generated with DesignSpark PCB - www.DesignSpark.com/pcb
--------------------------------------------------------------------------
Ref Name | Component | Value | Package | MPN
RESOLVER | 7 pin connector |  | USER | 22-04-1071
 | 7pin female housing |  |  | 22-01-1072
 | 6pin connector |  |  | 22-04-1061
 | 6pin female housing |  |  | 22-01-1062
 | crimp pins 13 of these!! |  |  | 08-50-0114
U1 | 7805Replacement |  | D2PAK | MC7812ABD2TG
C9 | Capacitor0.2-MLCC | 0.1uF | 1206Standard | C1206C104K5RACTU
C3 | Capacitor0.2-MLCC | 0.1uF | 1206Standard | C1206C104K5RACTU
C1 | Capacitor0.2-MLCC | 0.1uF | 1206Standard | C1206C104K5RACTU
C2 | Capacitor0.2-MLCC | 0.1uF | 1206Standard | C1206C104K5RACTU
C4 | Capacitor0.2-MLCC | 0.1uF | 1206Standard | C1206C104K5RACTU
C15 | Capacitor0.2-MLCC | 0.01uF | 1206Standard | 12065C103KAT4A
C14 | Capacitor0.2-MLCC | 0.01uF | 1206Standard | 12065C103KAT4A
C18 | Capacitor0.2-MLCC | 0.01uF | 1206Standard | 12065C103KAT4A
C22 | Capacitor0.2-MLCC | 0.01uF | 1206Standard | 12065C103KAT4A
C11 | Capacitor0.2-MLCC | 4.7uF | 1206Standard | CGA5L3X7R1H475K160AB
C19 | Capacitor0.2-MLCC | 4.7uF | 1206Standard | CGA5L3X7R1H475K160AB
C17 | Capacitor0.2-MLCC | 4.7uF | 1206Standard | CGA5L3X7R1H475K160AB
C23 | Capacitor0.2-MLCC | 4.7uF | 1206Standard | CGA5L3X7R1H475K160AB
C13 | Capacitor0.2-MLCC | 4.7uF | 1206Standard | CGA5L3X7R1H475K160AB
C25 | Capacitor0.2-MLCC | 4.7uF | 1206Standard | CGA5L3X7R1H475K160AB
C10 | Capacitor0.2-MLCC | 4.7uF | 1206Standard | CGA5L3X7R1H475K160AB
C20 | Capacitor0.2-MLCC | 30pF | 1206Standard | C1206C300J5GACTU
C21 | Capacitor0.2-MLCC | 30pF | 1206Standard | C1206C300J5GACTU
C12 | Capacitor0.2-MLCC | 2200pF | 1206Standard | VJ1206Y222MXXPW1BC
C16 | Capacitor0.2-MLCC | 2200pF | 1206Standard | VJ1206Y222MXXPW1BC
C26 | Capacitor0.2-MLCC | 2200pF | 1206Standard | VJ1206Y222MXXPW1BC
C8 | Capacitor0.2-MLCC | 2200pF | 1206Standard | VJ1206Y222MXXPW1BC
C24 | Capacitor0.2-MLCC | 2200pF | 1206Standard | VJ1206Y222MXXPW1BC
C7 | Capacitor0.2-MLCC | 2200pF | 1206Standard | VJ1206Y222MXXPW1BC
C6 | Capacitor0.2-MLCC | 2200pF | 1206Standard | VJ1206Y222MXXPW1BC
C5 | Capacitor0.2-MLCC | 2200pF | 1206Standard | VJ1206Y222MXXPW1BC
XTAL1 | CRYSTAL-8MHz | 8.192MHz | USER | XT9S20ANA8M
U2 | DualOpAmp |  | soicWithHeat | AD8397ARDZ-REEL7
J1 | encoder |  | USER | 22-04-1061
L1 | ferrite |  | 0805Standard | MMZ2012R102AT000
R1 | Resistor-0.25watt | 1k | 1206Standard | RK73H2BTTE1001F
R6 | Resistor-0.25watt | 1k | 1206Standard | RK73H2BTTE1001F
R8 | Resistor-0.25watt | 1k | 1206Standard | RK73H2BTTE1001F
R9 | Resistor-0.25watt | 1k | 1206Standard | RK73H2BTTE1001F
R11 | Resistor-0.25watt | 1k | 1206Standard | RK73H2BTTE1001F
R10 | Resistor-0.25watt | 1k | 1206Standard | RK73H2BTTE1001F
R2 | Resistor-0.25watt | 1k | 1206Standard | RK73H2BTTE1001F
R5 | Resistor-0.25watt | 1k | 1206Standard | RK73H2BTTE1001F
R4 | Resistor-0.25watt | 2.2k | 1206Standard | RK73H2BTTD2201F
R3 | Resistor-0.25watt | 2.2k | 1206Standard | RK73H2BTTD2201F
R7 | Resistor-0.25watt | 4.7k | 1206Standard | RC1206FR-074K7L
U3 | ResolverToEncoder-AD2S1210 |  | TQFP-48 | AD2S1210ASTZ

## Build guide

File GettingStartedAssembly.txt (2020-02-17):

Hello!  OK, let's start with the PDF.  The default is to use a hall effect throttle.  You can use either needle nose pliers and a little dab of solder, or a proper crimping tool like this (there may be a cheap chinese equivalent, but I'm not sure):
https://www.amazon.com/Engineer-PA-09-Micro-Connector-Crimpers/dp/B002AVVO7K

For the power section, I would suggest plugging in your board to 3 IGBT half bridges, and then placing the IGBTs/board on an aluminum plate and then mark the 12 IGBT holes.  Then you can drill the 12 holes with a hand drill and once they are fixed, all you need to do is add a B+ and B- copper sheet that bolts to the 3 B+ and B- points on the IGBTs (see the PDF).  I recommend making the copper sheets so the cross section is like this:  ][.  Then put an isolation between the 2 sheets.  Something like Kapton tape, or nomex paper.  So it would be like this:  ]|[.  ] would be B+, [ would be B-, and | would be the nomex paper or Kapton tape.  The idea is to bolt on the capacitor(s) upside down to B+ and B- sheets, and also bolt the sheets to all 3 IGBT half bridges.

I would suggest these capacitors in terms of easiness to work with:
http://www.mouser.com/ProductDetail/Kemet/C4DEFPQ6380A8TK/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

3 will fit, but It all depends on what power requirement you have.  Alternatively, I would get this:
http://www.sbelectronics.com/product/700d348-power-ring/
It's more mechanically awkward, but is capable of higher power.

next, decide what current sensors you are going to use.  What is the maximum current your motor will see?  I recommend Lem Hass 50-s, 100-s, 200-s, 300-s, 400-s current sensors.  Depending on the sort of current sensor and where you mount them, will determine how you will build your current sensor cables.  I suggest 3 of them for extra safety.

The board needs +24v for power.  To get that I would suggest this:
http://www.mouser.com/ProductDetail/Mean-Well/SD-15A-24/?qs=sGAEpiMZZMvGsmoEFRKS8N2RkxUSJnDinUf%252b7ghl12k%3d

Then you can use the car's +12v auxiliary battery for powering the DC-DC, which in turn powers the board.

 I'm putting together a video assembly, but it's not done.  One possible assembly process is here (specifically designed around the 16 tab ring capacitor):
http://www.instructables.com/id/200kW-AC-Motor-Controller-for-Electric-Car/

-Paul

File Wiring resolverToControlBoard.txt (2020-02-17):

Notice the writing for the pinouts for the resolver board.  The 7 pin connector goes:

See the attached ResolverToEncoder17Pinout.pdf.

The following goes to the resolver:
GND (this is optional, but would be connected to the shield of a 7 pin shielded cable).
!EX 
EX 
SIN+ 
SIN-
COS-
COS+

The following goes to the control/driver board:
+24v
+5v
GND
QEA
QEB
I (this is short of index)

On the control/driver board, see the pinout attached.  The view of the ACControlDriver26Pinout.pdf is of the top of the board, which is the surface mount components.  See the 6 connections on that board called:
Encoder +24v
Encoder +5v
Encoder GND
Encoder QEA
Encoder QEB
Encoder INDEX

Those pins go to the resolver to encoder board's 6 pin connector.

-Paul

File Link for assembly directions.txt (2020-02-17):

https://www.dropbox.com/s/7umzxa6tubatd9y/20170515_180213.zip?dl=0

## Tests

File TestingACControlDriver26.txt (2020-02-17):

Testing your newly soldered board:

Connect the 3 current sensors.

Jumper together J2/J3/J14, J7/J8/J15, and J11/J12/J4 (this disables the desaturation detection circuit, to allow the PWM to get through for testing)

Connect an AVRISP MKii (or some other avr programmer) to J41.  

Attach +24v to J38, and the 24v ground to J39.  
Program the ATTiny25 with DC-DC-Converter.hex.  You will need Atmel Studio, which is free, and something like an AVR isp mkii, or some other AVR programmer.
With power still attached, measure the voltage between each pair of back metal tabs of Q3/Q4, Q5/Q6, Q7/Q8, Q9/Q10, Q11/Q12, Q13/Q14.
You should get around 24v (+/-) for each measurement.  If you don't, check your soldering!
Disconnect 24v power.  Remove the AVRISP MKii.

Attach PICKit3.  
**Optional Extra step if you have MPLab installed, and can compile the AC controller software**
uncomment the line "#define DEBUG_MODE" in ACController.h.
Compile and program (in release mode) the dsPIC30F4011.  Measure the voltage from 0v to each of "GATE" across the top of the board. You should get around 3v each time.
Now, comment out the line "define DEBUG_MODE", so it looks like this:
// #define DEBUG_MODE
rather than
#define DEBUG_MODE
And then recompile the code and program the chip.  You are done!
**End of optional extra step**

Program the dsPIC30F4011 with the provided .hex file.  It will be called something like ACController.hex. Put the negative
probe of the volt meter on any of the test points across the top labeled 0v.  They are all connected right now because of the jumper wires you added.
With the positive lead of the volt meter, measure all the test points labeled "GATE". It should alternate -8v & 15v as you go left to right, measuring
"GATE" of all 6 isolated supplies.

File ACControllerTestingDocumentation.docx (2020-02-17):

AC Controller testing with Nissan Leaf Motor (or any motor that has a resolver whose lobes match the number of pole pairs of the motor)

If your control/driver board was completed by me, it has already been tested. First, let’s verify the wiring to the controller. This is a picture of the surface mount side of the most recent controller (ACControlDriver27.pcb):

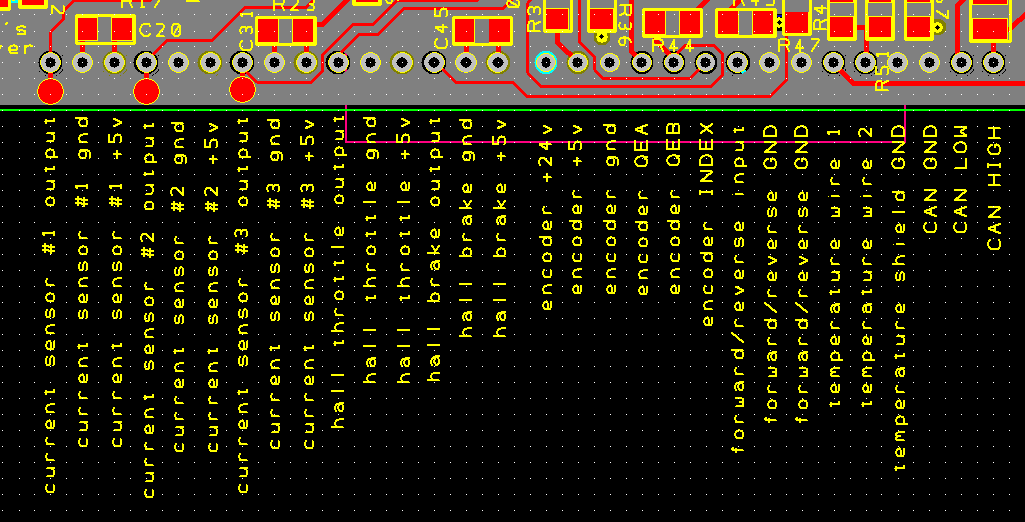
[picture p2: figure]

You need to build 3 current sensor cables. Let’s say you are using a LEM Hass 200-s. This will give a peak current range of -400amp to +400amp for the phases. Here’s the datasheet for the LEM Hass:

https://www.lem.com/sites/default/files/products_datasheets/hass_50_600-s.pdf

Pay attention to the pinout of the current sensor and the pinout of the control board. The current sensor has 4 pins, but you only need pin 2 (current sensor output), pin 3 (ground), and pin 4 (+5v). Pin 1 is not used, so there’s nowhere to plug it into the control board. So, you will need three 4 pin housings like this to mate to the 3 current sensors:

https://www.mouser.com/ProductDetail/Molex/22-01-1042?qs=5gBG3L055oM6gq%2fgjbx3Gw%3d%3d

And these pins:

https://www.mouser.com/ProductDetail/Molex/08-50-0114?qs=%2fha2pyFadujh2f7KQ%252bXWe2d6E0tCKKZpLCtYbdvIlLc%3d

The other end of the current sensor wire can use the same crimp pins too. You will need a total of 18 for the current sensor cables (none in the unused hole). Make sure you twist the 3 wires together for the current sensor cable to reduce noise. Use 22awg or 24awg wire. A drill works well for twisting the wires together. A shielded cable with the drain wire connected to the ground on one end works well too:

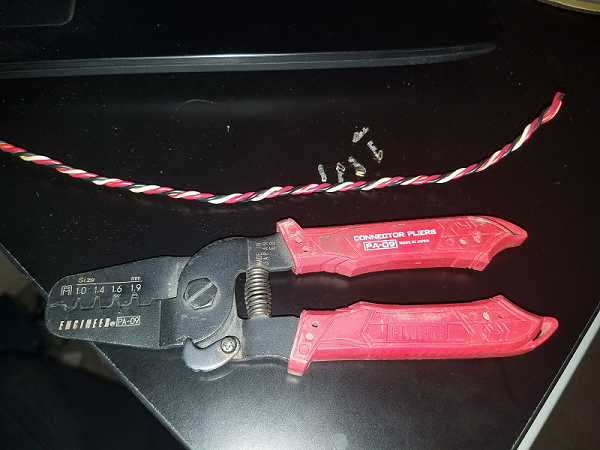
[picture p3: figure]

I use the 1.6 and the 1.9 mm for the crimping.

Next you will need a hall effect throttle like this:

https://www.ebay.com/itm/Throttle-PB-6-Type-0-5V-Hall-Effect-Throttle-Box-generic-/110658990971

You can get a 2nd one for the brakes if you like, but as of ver. 1.0 of the software, the brake regen is disabled. You only get regen from releasing the throttle. The brake regen will be added most likely in the next software release.

If you are using a resolver to encoder board, you will need to connect the 6 encoder pins on the control board (+24v, +5v, gnd, QEA, QEB, INDEX) to the resolver to encoder board:

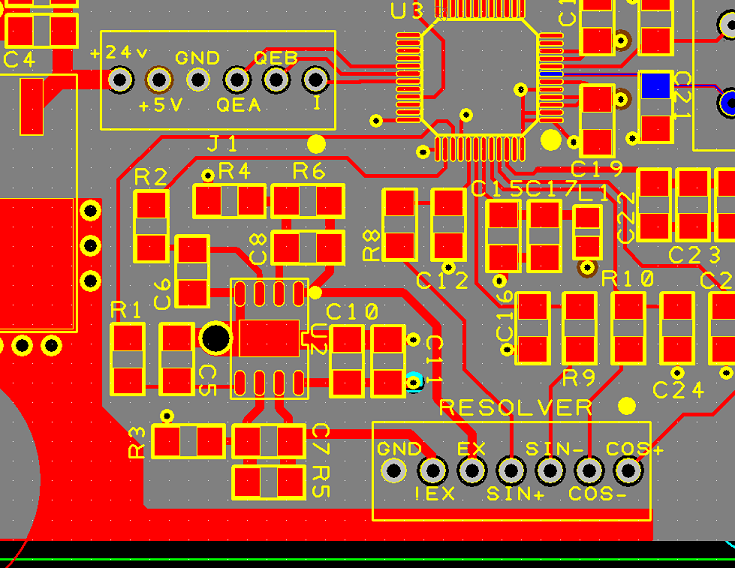
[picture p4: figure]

You will then also need to connect the !EX, EX, SIN+, SIN-, COS-, COS+ pins of the resolver-to-encoder board to the resolver on the motor. Each motor is different, but here’s the pinout for two types of Nissan Leaf motors (2011 and 2012?):

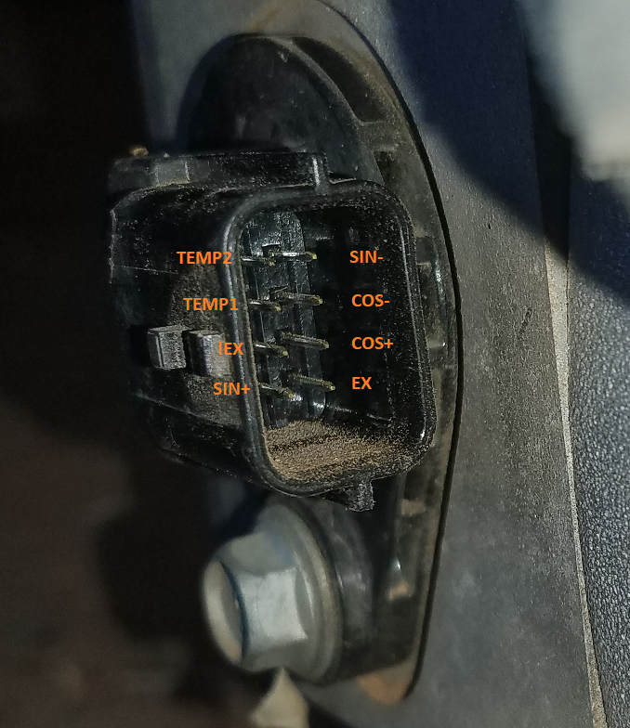
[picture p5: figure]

Next is the forward/reverse pin. This is unimplemented right now, but should be functional in version 1.1. You will need a simple toggle switch (SPST). Flipped one way, the motor will rotate one direction, and flipped the other way will cause the motor to turn the other direction. There are a total of 3 pins for the forward/reverse pin. This is to allow you to use one of the forward/reverse GND connections for an optional shield for the forward reverse cable.

Next is temperature wire 1, and temperature wire 2. Hook up a thermistor like this one to the aluminum base plate, and then connect it to those 2 pins of the controller:

https://www.mouser.com/ProductDetail/Vishay-BC-Components/NTCALUG03A103GC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

All that matters is that the B parameter is about 3984K and it is a 10k thermistor. Temperature shield GND is an optional pin for for the shield of the thermistor wires, if you use a shielded cable.

The next 3 pins are CAN GND, CAN LOW, CAN HIGH. This is unimplemented as of version 1.0. In order to use CAN at a standard bit rate such as 250kbps, the crystal oscillator (XTAL1) needs to be switched from 7.3728MHz to a 7.5MHz crystal, and also the USB data rate needs to be reduced to 38.4kbps.

Now for the spade connection wiring:

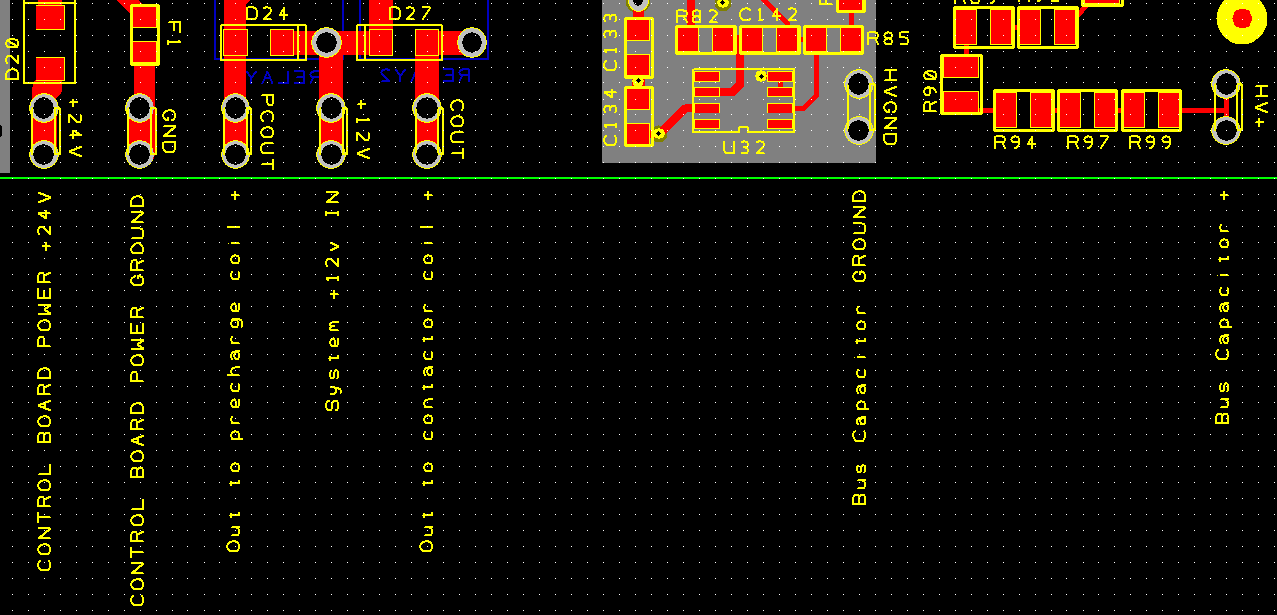
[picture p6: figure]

Using a DC/DC such as this, set the output (there’s a pot on the DC/DC) to about 24 to 25vDC:

https://www.mouser.com/ProductDetail/MEAN-WELL/RSD-60G-24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

Connect the pin labeled +24V to the +24v on the DC/DC. Connect the 24vDC ground to the pin labeled GND. Connect PCOUT to the positive side of the precharge relay coil.

For a precharge relay, I would suggest the P115-BDA from Gigavac:

http://www.gigavac.com/sites/default/files/catalog/spec_sheet/p115.pdf

For a precharge resistor, I would suggest something like this:

https://www.mouser.com/ProductDetail/Ohmite/AZ151KE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

Connect the negative side of the precharge and contactor coils to the 12v system ground (usually a car has a system voltage of +12v. Pick a contactor that will energize from 12vDC). On the pin labeled +12V, connect the car’s +12v. Connect COUT to the positive side of the main contactor’s coil. For a main contactor I would suggest this (the one that has a 12v coil):

http://www.gigavac.com/sites/default/files/catalog/spec_sheet/gv200.pdf

Next, connect the bus capacitor’s high voltage ground to HVGND, and the bus capacitor’s high voltage positive to HV+ on the control board. This is for DC voltage monitoring, as well as introducing a bleeder resistor into the system.

Next, the 3 IGBTs plug directly into the control/driver board (directly underneath the PCB):

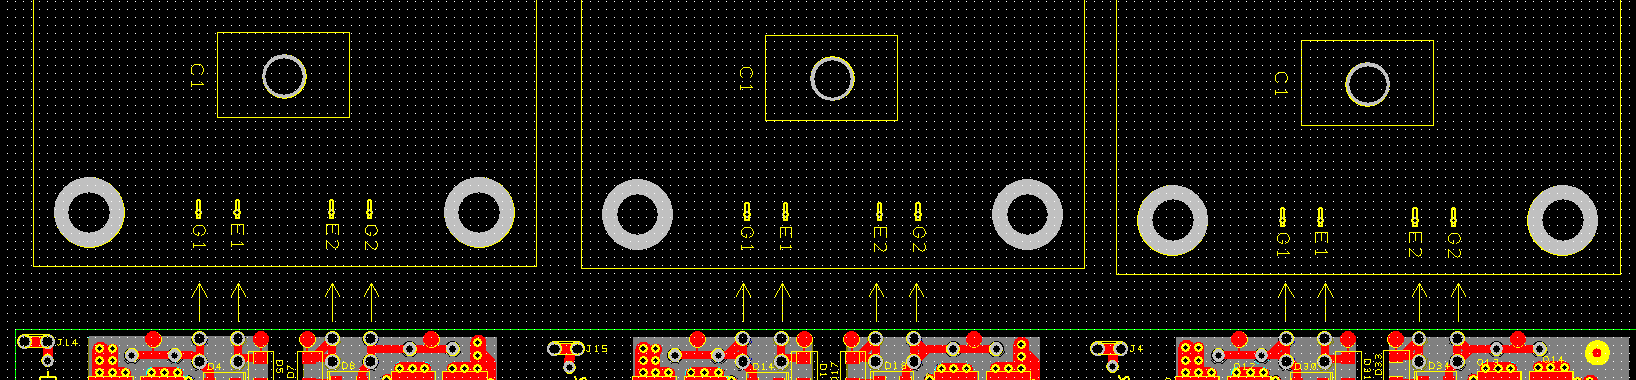
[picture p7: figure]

Next, the 3 connectors labeled J4, J14, J15 get connected to the bus capacitor +. That’s all the wiring!

Debugging:

To verify that the control/driver board is working like it should, make sure the high voltage is disconnected, and load the file debugging.hex that is included with this .zip package (see the section of this document titled “Programming” to see how to program the chip). Then, measure the 6 rows of 3 test points per row across the top of the board (each row is labeled -8v, 0v, 15v). There are 3 test points on the left and 3 on the right of each “-8v”, “0v”, “15v”. There will be a row of those 3 test points repeated 6 times across the top of the board, for each of the 6 supplies. Measure from 0 to -8v, and 0v to 15v for each of those 6 “three hole rows” to verify that all 6 supplies are working. Next, measure from “gate” to “0v” across the top of the control/driver board (measure all 6 pairs of those) and verify that you are getting about +3v from “gate” to “0v” for each of those 6 supplies. If those are good, program the board with the .hex file attached to this .zip package.

Now, to test that the throttle is working, in realterm type:

stream-raw-throttle 1

Data-stream-period 100

Now, turn the throttle all the way down, and note the number for the raw throttle (between 0 and 1023). Next turn the throttle all the way to 100%, and note the number for the raw throttle. To stop the stream, just type “off”. Let’s say that your low and high numbers were 85 and 879. Then, a good configuration for the throttle mapping would be to type the following in realterm:

max-regen-position 85

min-regen-position 220

min-throttle-position 300

max-throttle-position 879

save

That would set the throttle map so that 0% throttle gives the maximum regen current, 220 would be the starting point for the regen, 300 would be the start of the positive torque, and 879 would be the maximum torque.

To verify that the resolver to encoder board is working correctly with the control board, connect the resolver to encoder board to the motor, and to the control board. Then, with no high voltage attached, connect the control board to Realterm using the USB plug on the board. The settings are 115200bps, 8N1 (8 data bits, no parity, and 1 stop bit) :

https://sourceforge.net/projects/realterm/

Then, turn on the 24v power to the control board. Then, type the following in Realterm:

stream-rotor-flux-angle 1

data-stream-period 100

Then, turn the motor shaft by hand, and you should see the rotor flux angle go from 0 to 511, and then start over again at 0 (or it might go backwards).

Connecting the IGBTs to the outside world:

In the picture below, B+ goes to the bus capacitor plus, and also to the main contactor. The other side of the main contactor goes to a fuse. The other side of the fuse goes to the high voltage battery pack +. B- can go straight to the bus capacitor -, and also to the high voltage battery pack -. U, V, and W goes to U,V,W on the 3 phase motor. B+ also goes to one side of a precharge relay. The other side of the precharge relay goes to one side of a precharge resistor. The other side of the precharge resistor goes to the high voltage battery pack +. For setting the precharge time in realterm, you go like this:

precharge-time 47

save

That would set the precharge time to 4.7 seconds. Let’s say you choose a precharge resistor that is 470 Ohms, and your bus capacitance is 1000 microFarad. For your precharge time, it would be:

5*R*C = 5 * 500 * 1000*10^-6 = 2.5 seconds. So, you would set the precharge time to 2.5 seconds in that case.

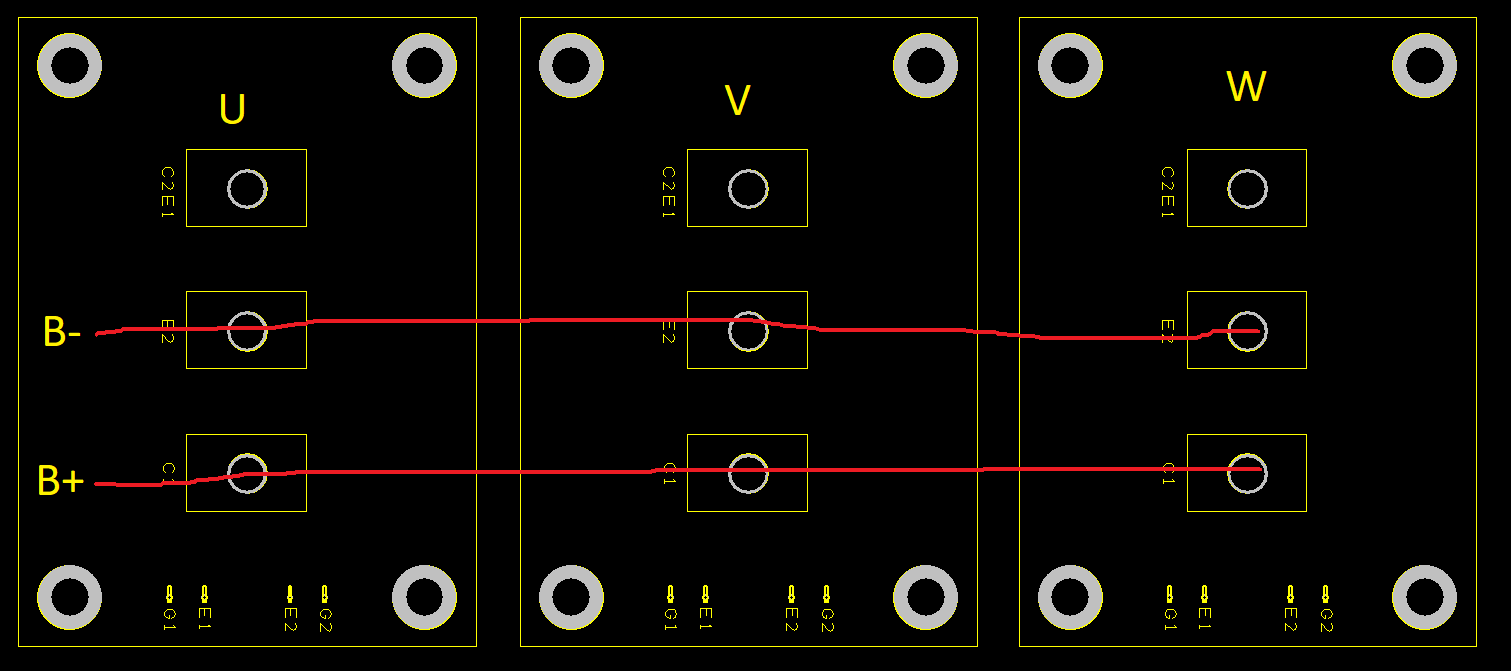
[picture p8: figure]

This is one possible way of connecting the bus capacitor(s) to the IGBTs. You can do it however you want. All that matters is, the “loop area” from B+ on the IGBTs to the capacitor + to the capacitor – to the B- on the IGBTs is as small as possible. That’s why copper sheets are used, and why they are sandwiched together like that.

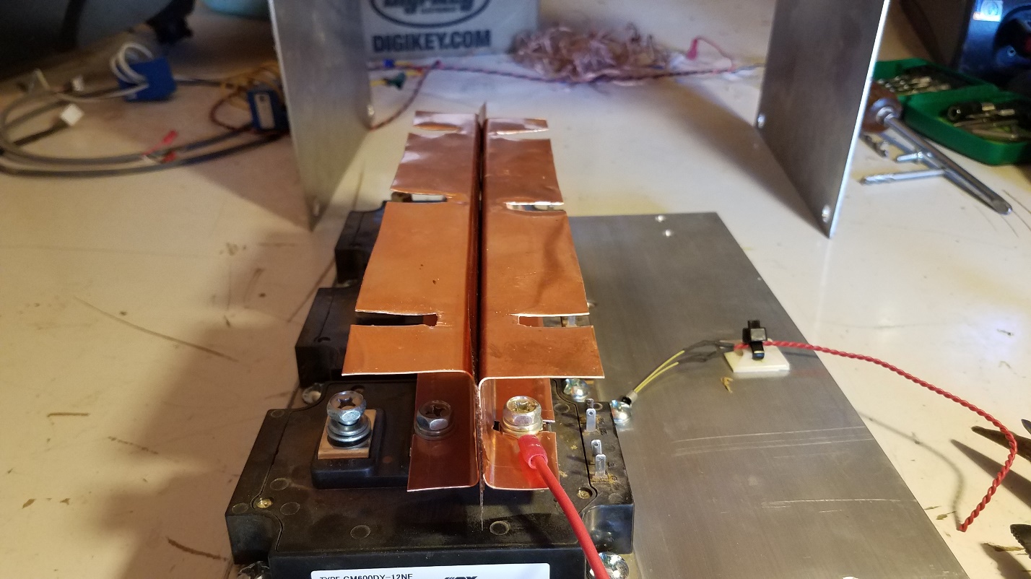
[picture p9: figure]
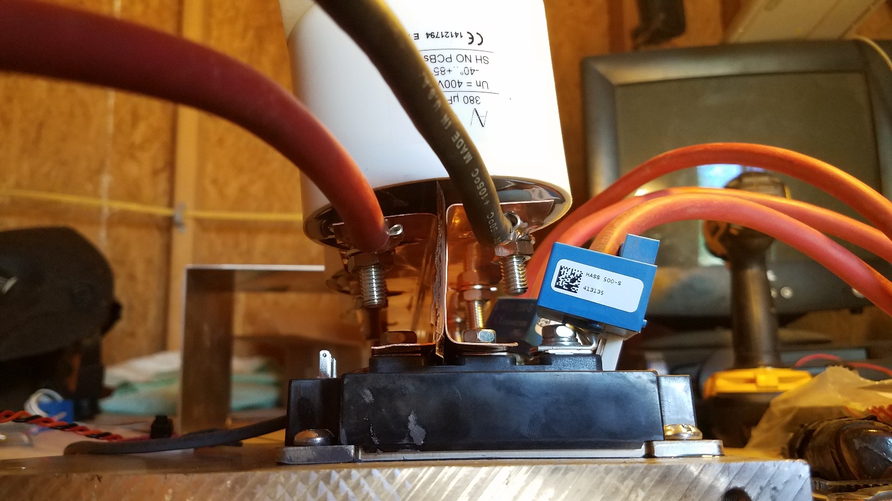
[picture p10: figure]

Notice that the current sensors go on each of the 3 phase cables (U/V/W) to the motor. NO! YOU CANNOT USE 2 OF THEM WITHOUT MODIFYING THE CONTROL/DRIVER BOARD! 😊

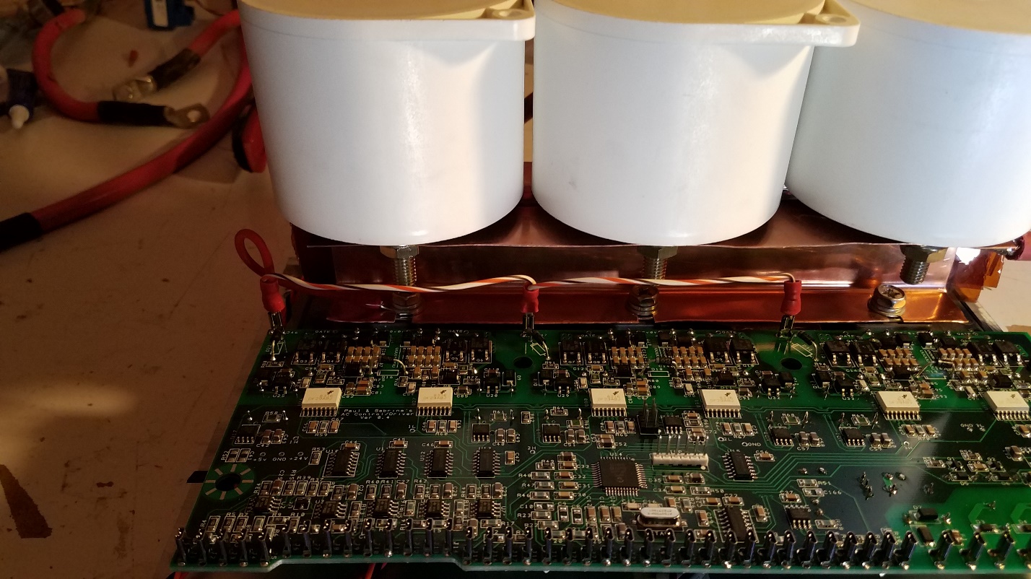
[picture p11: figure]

Notice in the above picture how the high voltage B+ connects to the 3 points on the control/driver board.

Programming:

Reprogramming the dsPIC30F4011 microcontroller using MPLab X:

If you want to change the flash memory of the microcontroller, do the following:

1. Download MPLab X. Click on File -> Import -> Hex/Elf… (Prebuilt) file
2. Choose your .hex file and select “Pickit 3” from the hardware tool section. Click Next…
3. Set the active project. Click finish.
4. Plug the pickit 3 into the control/driver board at the 6x1 pin vertical connector that just has 6 bare pins sticking out next to the microcontroller. Make sure that the white triangle on the pickit 3 matches up with the white dot on the control/driver board (pin 1). Also plug the pickit 3 into the computer.
5. Turn on the 24v power to the control/driver board.
6. Click on the icon that says “Make and Program Device Main Project” when you hover the mouse over it.

Here’s a helpful demonstration with pictures, and a video:

http://jeffeblack.com/writing-software-to-the-microprocessor-in-the-diy-leaf-control-board-from-ps/

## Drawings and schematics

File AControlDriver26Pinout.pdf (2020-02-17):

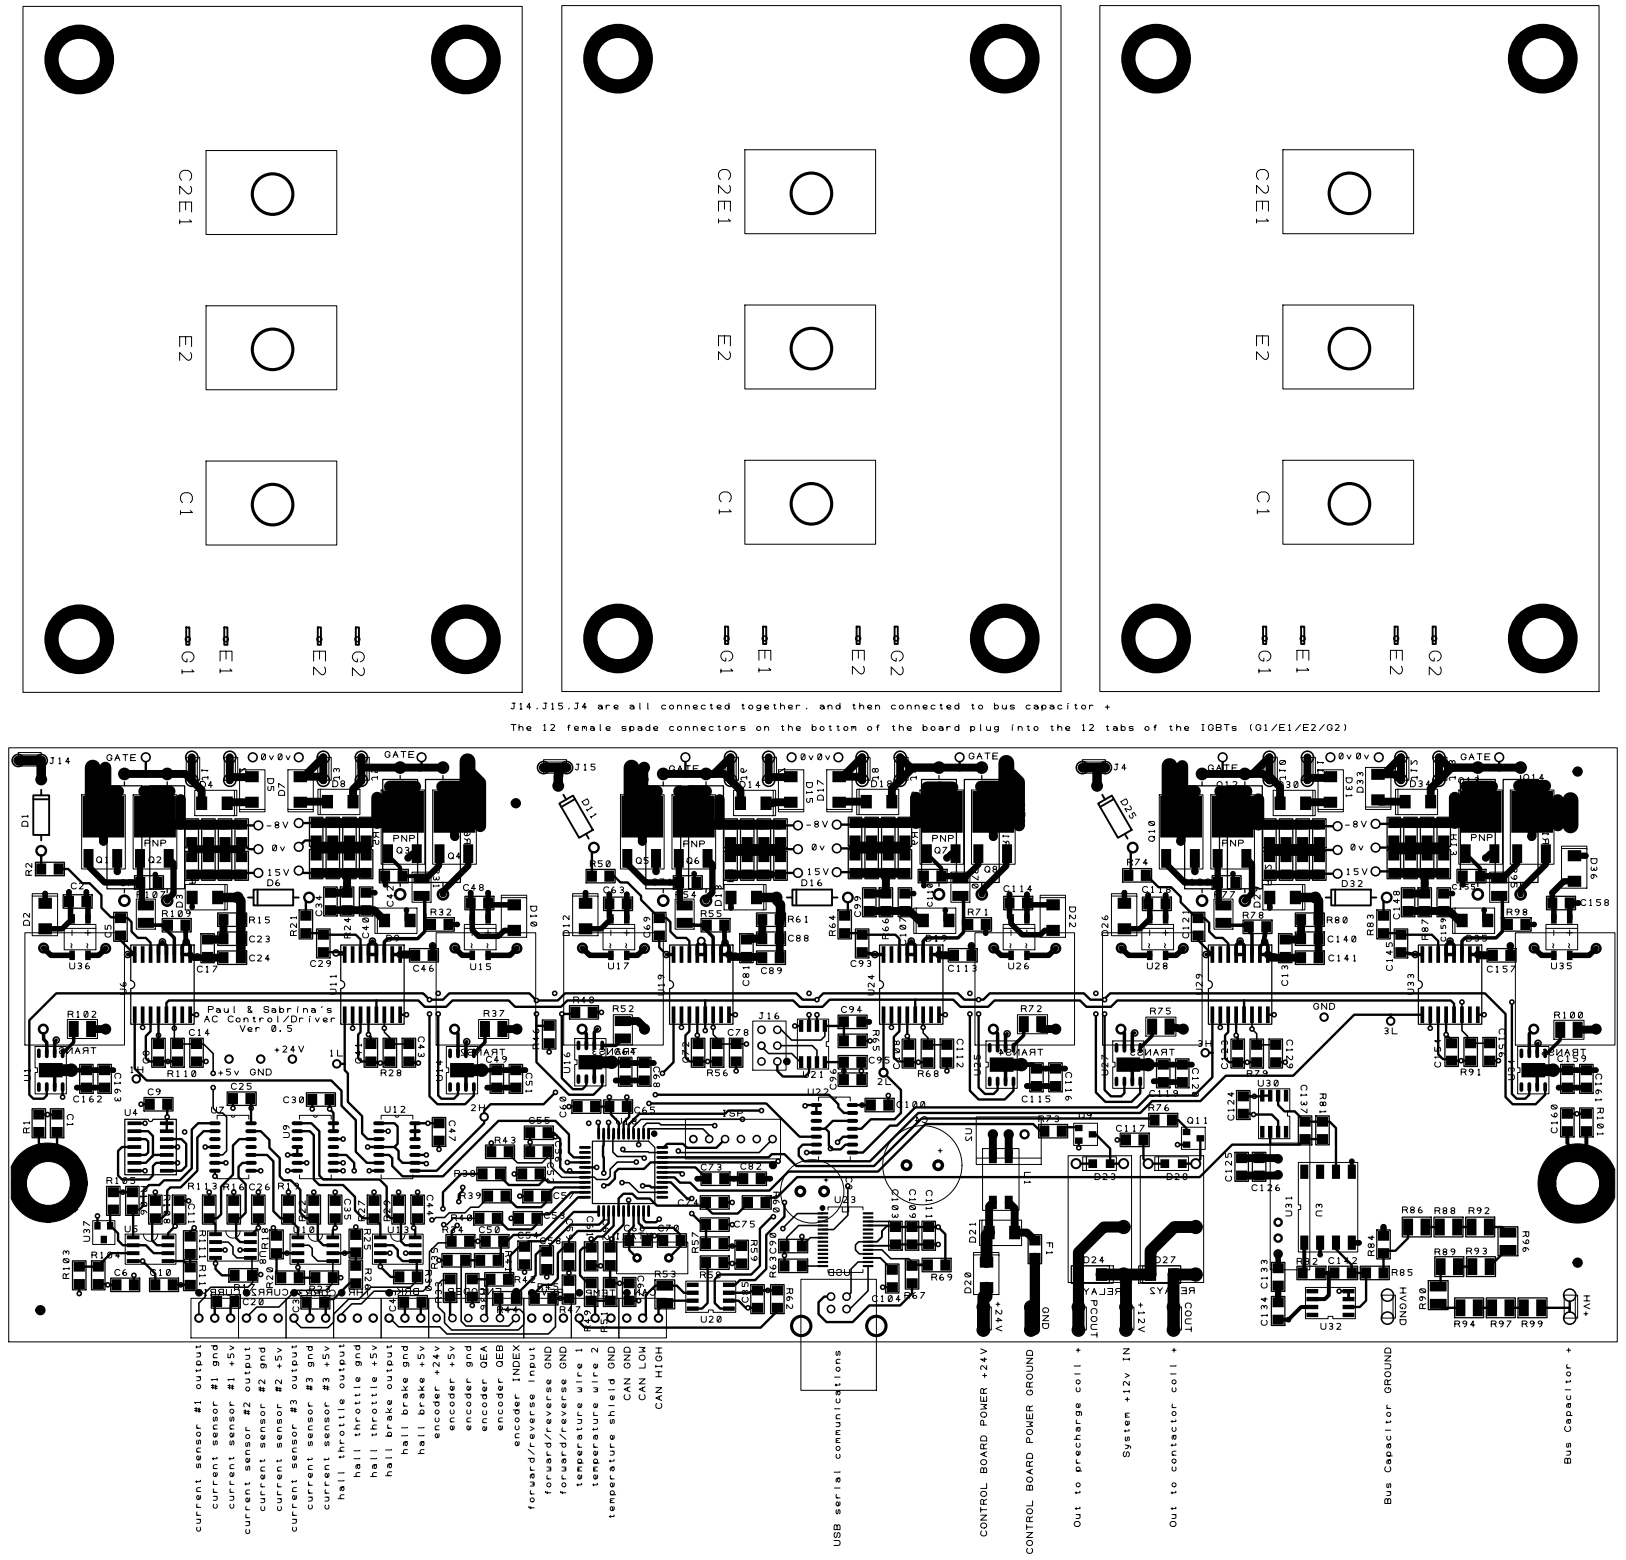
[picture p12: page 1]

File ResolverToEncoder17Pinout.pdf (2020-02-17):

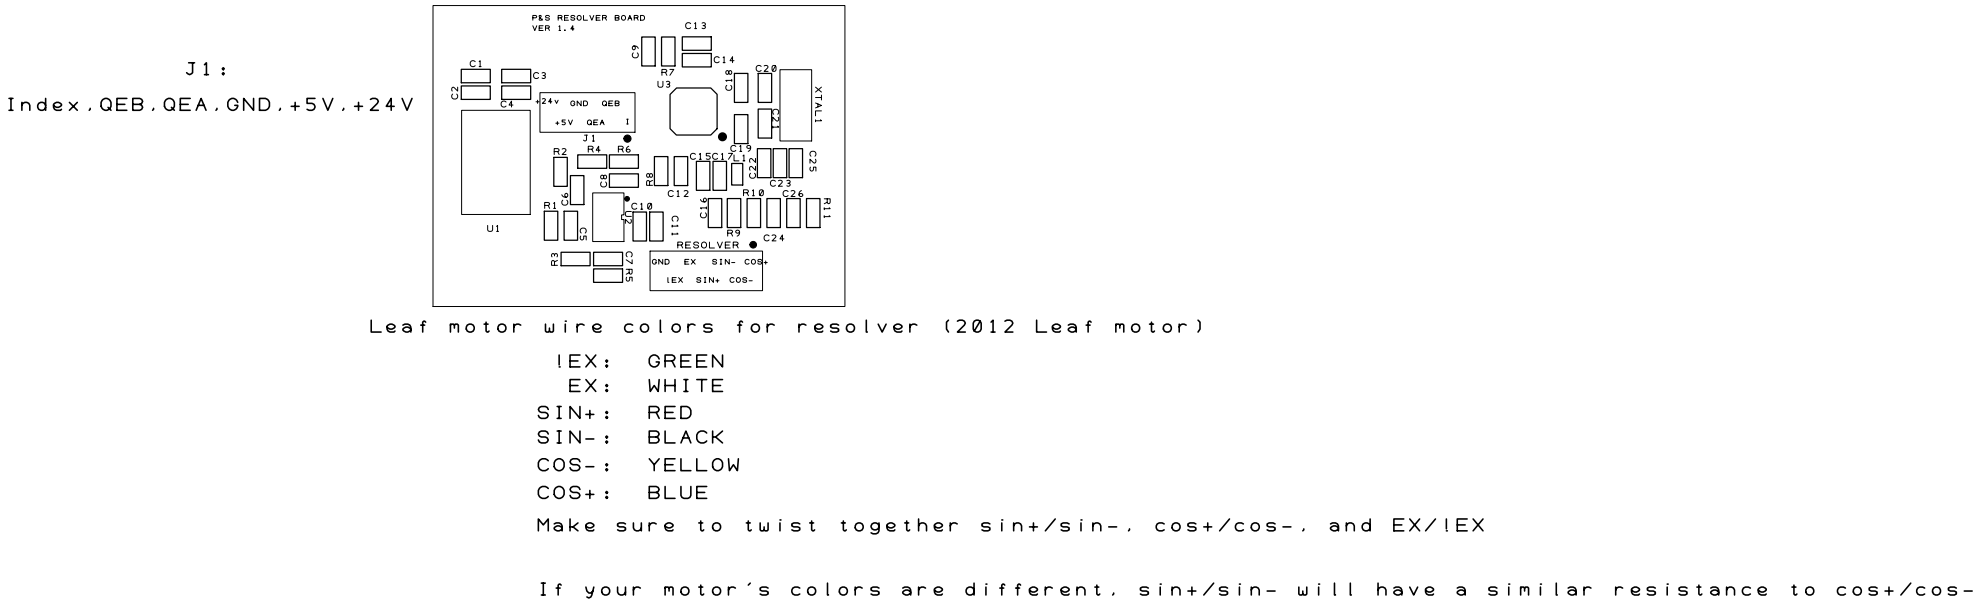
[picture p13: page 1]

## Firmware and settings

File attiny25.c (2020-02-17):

#include <stdio.h>
#include <avr/wdt.h>
#include "attiny25.h"

void InitIOPorts();
void watchdog_disable();
void watchdog_enable();

int main(void) {
	watchdog_enable();
	InitIOPorts();
	while (1) {


		// Set port B3 and B4 to their complements.
//		PORTB ^= ((1 << PB3) | (1 << PB4));  // When one is low, the other is high.  Swap them here.
		PORTB = 0b10111;
		asm("nop");asm("nop");asm("nop");
		PORTB = 0b01111;


		wdt_reset();
	}
	return 0;
}

void InitIOPorts() {
	DDRB = 0;			//  all are inputs at this stage.
	PORTB = 0b11111;  	// turn on all pull up resistors.
	asm("nop");
	DDRB = 0b11000; 	// make PB3 and PB4 outputs.
	//DDRB |= (1 << PB3);    // Data direction register.  Set to 1 to configure as outputs.
	//DDRB |= (1 << PB4);		// PB4 is also an output.
	//PORTB
	//PORTB &= ~(1 << PB3);   // Use PORTB to set the value of pins when they are outputs. PB3 starts as 0.
	//PORTB |= (1 << PB4);    // Start PB4 as 1.
}


void watchdog_disable(void)
{
	wdt_reset();
	wdt_disable();
}

void watchdog_enable(void)
{
	wdt_reset();
	wdt_enable(WDTO_15MS);
}

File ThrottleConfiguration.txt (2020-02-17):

throttle configuration:

throttle fault < max regen < min regen < min positive torque < max positive torque

So, a possible configuration for a standard hall effect throttle would be:

throttle fault = 5
max regen = 50
min regen = 200
min positive torque = 250
max positive torque = 900

So, "zero torque command" is in 200-250.  Then, when you release the throttle completely, it might show 50 on the microcontroller, so you would get max regen until you come to a stop.
Full throttle would be around 900 (1023 would mean 5.0 volts for the analog signal).
